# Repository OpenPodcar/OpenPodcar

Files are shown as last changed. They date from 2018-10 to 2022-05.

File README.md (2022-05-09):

# OpenPodcar

Open Source Hardware Design and Software for OpenPodcar.

https://user-images.githubusercontent.com/34858915/167230498-64ceeedd-7fe7-4e6d-a8b0-ddad5ff45466.mov

## Table of Contents
I. [General Info](#general-info)

II. [Bill of Materials](#bom)

III. [Software Setup](#software-setup)

IV. [Hardware Setup](#hardware-setup)

V. [User Guide](#user-guide)

VI. [General Testing](#general-testing)

VII. [3D Gazebo Simulation](#gazebo-simulation)

VIII. [Troubleshooting Guide](#troubleshooting-guide)

IX. [How to Contribute?](#how-to-contribute)

X. [Cite OpenPodcar](#cite-openpodcar)

XI. [Licence](#licence)

## I.  General Info

The OpenPodcar is an affordable and open source hardware and software platform for self-driving car research. It can be used for general autonomous vehicle research as well as for human-robot interaction (HRI) studies and practical automated transportation of people and goods.

The project includes:
- Hardware design and instruction to build and wire the physical car
- Arduino software for speed control
- Pololu software for steering control
- ROS drivers for the whole vehicle steering and speed
- Gazebo 3D simulation
- move_base and gmapping integration

To build the physical OpenPodcar, first obtain the components detailed in [Bill of Materials](#bom), then follow the steps of the build process detailed in [Software Setup](#software-setup), [Hardware Setup](#hardware-setup),  [General Testing](#general-testing) and [User Guide](#user-guide). The 3D simulation can be directly installed in [3D Gazebo Simulation](#simulation).

## II.  Bill of Materials
Obtain the following components, which are available from many commercial suppliers and some weblinks are suggested.

### 1. For the vehicle
- 1 Pihsiang TE-889XLSN hard-canopy scooter (branded in UK as ShopriderTraverso) e.g. [Link to product](https://romamedical.co.uk/shoprider-traveso/)
- 1 3D Velodyne Lidar (VLP-16) with its controller box e.g. [Link to product](https://velodynelidar.com/products/puck/)
- 1 laptop under linux Ubuntu 16.04 e.g. [Link to product](https://www.lenovo.com/gb/en/laptops/thinkpad/p-series/ThinkPad-P51/p/22TP2WPWP51)
- 1 Laptop or computer under Windows 7+
- 1 Gimson Robotics GLA750-P 12V DC linear actuator with position feedback (250mm stroke) e.g. [Link to product](https://gimsonrobotics.co.uk/categories/linear-actuators/products/gla750-p-12v-dc-linear-actuator-with-position-feedback)
- 1 ON/OF Toggle/Flick switch button e.g. [Link to product](https://www.ebay.co.uk/itm/12V-HEAVY-DUTY-25A-UNIVERSAL-METAL-SPRING-MOMENTARY-ON-OFF-TOGGLE-FLICK-SWITCH/231257116468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)
- 1 USB hub (with at least 3 USB ports) e.g. [Link to product](https://www.amazon.co.uk/AmazonBasics-4-Port-Ultra-Mini-Bus-powered/dp/B003M0NURK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)
- 1 USB A cable (Arduino <-> Laptop)
- 1 USB mini B cable (Pololu <-> Laptop)
- 1 Ethernet cable (Velodyne <-> Laptop) 
- 1 Deadman push button for the vehicle ignition system e.g. [Link to product](https://www.ebay.co.uk/itm/Philmore-30-825-SPST-Hand-Held-Push-Button-Switch-N-O/253746249505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)
- 1 3-meter rubber cable e.g. [Link to product](https://www.design-restoration-spares.com/product/real-rubber-cable-3-core-black/) 
- 1 Joystick with its USB cable e.g. [Link to product](https://www.logitechg.com/en-gb/products/space/extreme-3d-pro-joystick.942-000031.html)
- 1 Manfrotto Black Digi Table Tripod 709B e.g. [Link to product](https://www.manfrotto.com/ie-en/black-digi-table-tripod-709b/)
- 1 Inline car fuse e.g. [Link to product](https://www.ebay.co.uk/itm/BRAND-NEW-STANDARD-INLINE-CAR-FUSE-BLADE-HOLDER-30AMP-12V-SPLASH-PROOF-K265/170976134151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)
- 1 Fuse 7.5Amp
- 1 Relay e.g. [Link to product](https://www.ebay.co.uk/itm/164139969972?hash=item2637812db4:g:LqAAAOSwX9VefSO4)
- A few metric HEX bolts, nuts, flat washers and cap nuts
- A few cables ties

### 2. For the PCB
- 2 XL4016 Step-Down Buck converters DC-DC e.g. [Link to product](https://www.amazon.co.uk/dp/B086W6B9H1/ref=pe_27063361_485629781_TE_item?th=1)
- 1 Arduino Uno Rev3 e.g. [Link to product](http://store.arduino.cc/products/arduino-uno-rev3)
- 1 Pololu JRK 21v3 Motor Controller with Feedback e.g. [Link to product](https://coolcomponents.co.uk/products/jrk-21v3-usb-motor-controller-with-feedback-fully-assembled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)
- 1 MCP4725 DAC e.g. [Link to product](https://protosupplies.com/product/mcp4725-12-bit-dac-module/)
- 1 7-segment LCD with 3 digits e.g. [Link to product](https://www.alibaba.com/product-detail/Taidacent-Red-0-200V-Measurement-Range_60679181399.html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)
- 1 Velodyne controller box (comes with the Velodyne lidar)
- 1 10K Resistor
- 1 100K Resistor
- 2 Screw Terminal Block connectors e.g. [Link to product](https://www.amazon.co.uk/Universal-Connector-Calculators-Electronic-Equipments/dp/B0922KLC4K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)
- Male and female headers for Arduino and Pololu JRK 21v3 e.g. [Link to product](https://www.amazon.co.uk/dp/B07CWSXY7P/ref=pe_27063361_485629781_TE_item)
- A few M1.5, M2.5 and M3 bolts and nuts 

### 3. Tools
- Soldering station with solder
- Female and Male insulated electric connector crimp bullet terminals e.g. [Link to product](https://www.aliexpress.com/item/32874324815.html)
- Female and Male insulated crimp bullet terminals e.g. [Link to product](https://www.ebay.co.uk/itm/333917138391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)
- Power supply 24V or more e.g. [Link to product](https://www.amazon.co.uk/Lavolta-Variable-Linear-Bench-Supply/dp/B019KL4G6I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)
- Breadboard e.g. [Link to product](https://www.amazon.co.uk/K-H-RH-32-Solderless-Breadboard/dp/B07DNB74FV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)
- Multimeter e.g. [Link to product](https://www.machinemart.co.uk/p/clarke-cdm10c-digital-multimeter-5-function/)
- Gauge wires e.g. ~0.8mm, ~2mm and ~4mm diameter
- ELEGOO 120pcs Multicolored Dupont Wires 40pin Male to Female, 40pin Male to Male, 40pin Female to Female Breadboard Jumper Wires Ribbon Cables Kit Compatible with Arduino Projects [Link to product](https://www.amazon.com/Elegoo-EL-CP-004-Multicolored-Breadboard-arduino/dp/B01EV70C78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)
- Clamp meter e.g. [Link to product](https://www.tester.co.uk/uni-t-ut210b-clamp-meter)
- Flathead and Phillips screwdrivers, pliers and automatic wire stripper
- Spare fuses e.g. [Link to product](https://www.halfords.com/tools/fuses-electricals-and-fixings/fuses/)

## III.  Software Setup

### 1. Ubuntu 16.04 and ROS

The OpenPodcar software stack requires a laptop working under Ubuntu 16.04 and with ROS Kinetic and Gazebo 7 installed:
- [Ubuntu 16.04 installation](https://ubuntu.com/tutorials/install-ubuntu-desktop#1-overview)
- [ROS Kinetic + Gazebo 7 installtion](http://wiki.ros.org/kinetic/Installation/Ubuntu)
- Clone this project repository somewhere on the laptop

**NB:** `Pololu JRK Configuration Utility` tool is a Windows app, which does not work on linux.

### 2. Arduino
- Install Arduino IDE on the Ubuntu laptop, instructions can be found [here](https://ubuntu.com/tutorials/install-the-arduino-ide#1-overview)
- Download the MCP4725 library file and place it into Arduino's `LIBRARIES` folder
- Arduino firmware source is supplied in `physicalVehicleNonRos/Arduino/ThrottleControlSerial.ino`
- Connect the Arduino USB cable to the laptop
- Open the `ThrottleControlSerial.ino` file in Arduino IDE
- Click on "**Upload**"
- **Acceptance Testing**
	- click on "**Tools**", then "**Serial Monitor**" 
	- set baudrate to 115000
	- type in some commands such as:
		- "**FA:170**" for zeroing
		- "**FA:210**" for forward speed
		- "**FA:120**" for reverse speed
	- the serial monitor should display the command that was typed in and the corresponding DAC value
	
### 3. Pololu JRK 21v3 Configuration

- Download Pololu's Windows Configuration Tool `Pololu JRK Configuration Utility` on a Windows  computer by following these steps [here](https://www.pololu.com/docs/0J38/3.a).
- To configure the Pololu, please follow the instructions [here](https://www.pololu.com/docs/0J38/5).
- For OpenPodCar, the steps below are followed:
	- Connect the Pololu USB cable to the Windows computer and open `Pololu Jrk Configuration Utility` tool

	- Go to "**Input**" tab: 
		- set "**Input mode**" to "**serial**"
		- keep all other parameters to default values
		- Final settings should like in the figure below:
		
	<p align="center">
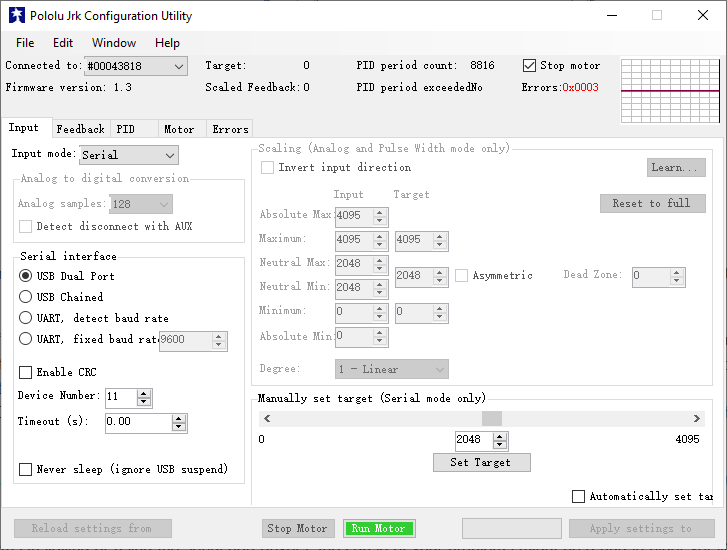
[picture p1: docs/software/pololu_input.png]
Pololu Input tab
	
	</p>

	- Go to "**Feedback**" tab:
		- set "**Feedback mode**" to "**Analog voltage**"
		- check "**Invert feedback direction**"
		- Under "**Calibration**":
			- set "**Absolute Max**" to "**2600**"
			- set "**Maximum**" to "**2600**"
			- set "**Minimum**" to "**1000**"
			- set "**Absolute Min**" to "**1000**"
			- keep all other paramters to default values
		- Final settings should like in the figure below:
	
	<p align="center">
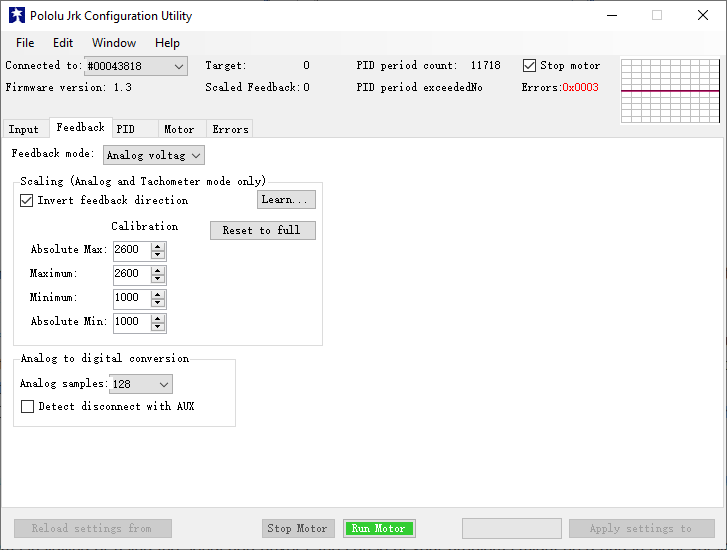
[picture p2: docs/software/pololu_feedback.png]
Pololu Feedback tab
	
	</p>

	- Go to "**PID**" tab:
		- set "**Proportional Coefficient**" to "**6**" at the top and "**1**" at the bottom, so that to get a final "**3**"
		- keep all other parameters to default values 
		- Final settings should like in the figure below:

	<p align="center">
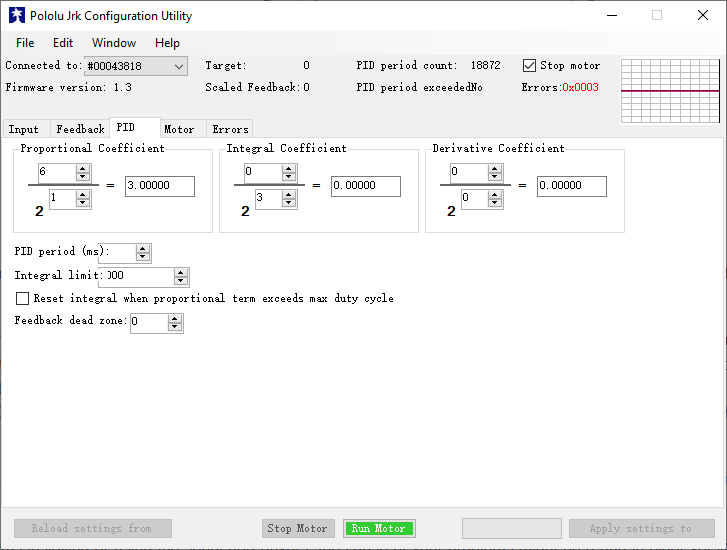
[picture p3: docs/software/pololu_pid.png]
Pololu PID tab
	
	</p>

	- Go to "**Motor**" tab:
		- check "**Invert motor direct**"
		- in the "**Forward column**", set "**Max. current (A)**" to "**0**"
		- keep all other parameters to default values
		- Final settings should like in the figure below:
		
	<p align="center">
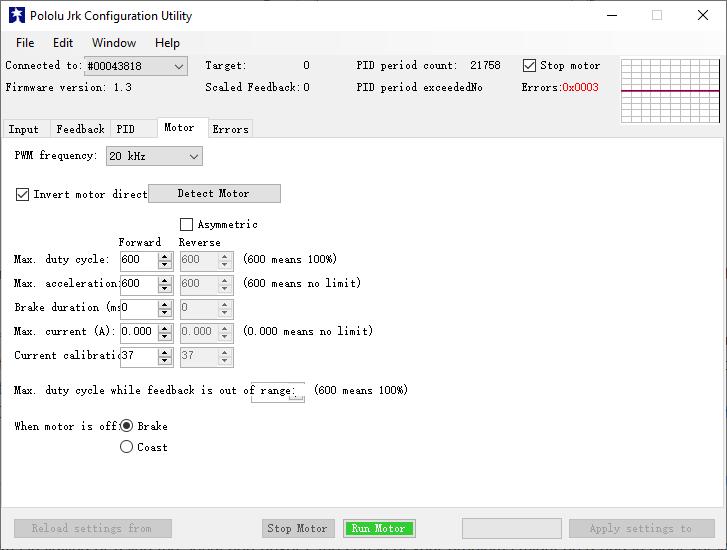
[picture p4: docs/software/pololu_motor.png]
Pololu Motor tab
	
	</p>

	- Go to "**Error**" tab:
		- you should see a window similar to the figure below with some red flags on	
		- set "**No power**", "**Motor driver error**", "**Feedback disconnected**" and "**Max. current exceeded**" to "**Enabled and latched**"
		- click on "**Clear**" and "**Reset**"
		
	<p align="center">
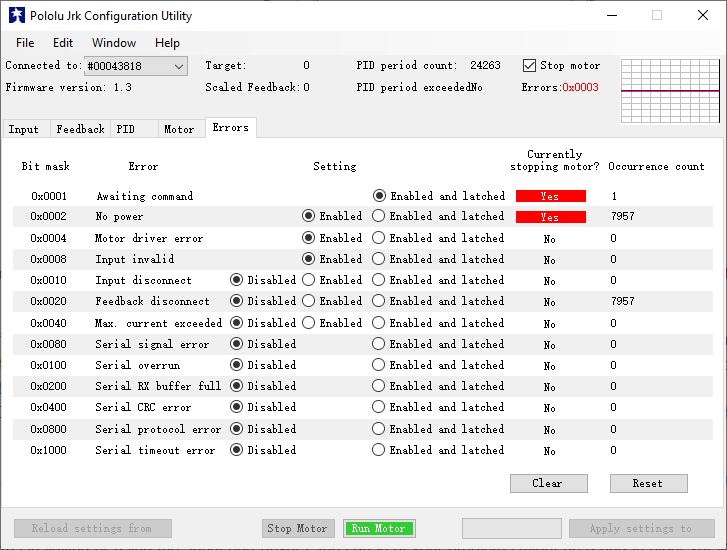
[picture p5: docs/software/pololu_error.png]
Pololu Error tab
	
	</p>

	- Click on "**Apply settings to**"

### 4. Simlink for USB COM Ports

Here, the goal is to create persistent USB serial device names (aka Simlink) for the Arduino and the Pololu.

- In a terminal, type: `sudo nano /etc/udev/rules.d/99-tty.rules`
- Connect the Arduino and the pololu USB cables to the linux laptop using a USB hub, then type in the terminal:
```
sudo lsusb -v | grep 'idVendor\|idProduct\|iSerial'
```
- The above command displays the idVendor and idProduct for all the serial devices connected to your laptop and needs to be reported in the Simlink. 
- Copy the following lines in `99-tty.rules` file:
```
#Arduino com-port rules
SUBSYSTEM=="tty", ATTRS{idVendor}=="2341", ATTRS{idProduct}=="0043", SYMLINK+="ttyArduino", GROUP="dialout", MODE="0666"
#Pololu com-port rules -- NB the pololu has two virtual serial ports on a single USB interface.
SUBSYSTEM=="tty", ATTRS{idVendor} =="1ffb", ENV{ID_USB_INTERFACE_NUM}=="00"  SYMLINK+="ttyPololuCOM"
SUBSYSTEM=="tty", ATTRS{idVendor} =="1ffb", ENV{ID_USB_INTERFACE_NUM}=="02"  SYMLINK+="ttyPololuTTL"
```
- Save and close `99-tty.rules` file
- Then type in the terminal `sudo reboot`
- Check the status of each SimLink by typing in terminal for example: `ls -l /dev/ttyArduino` or `ls -l /dev/ttyPololuCOM`

### 5. Velodyne 3D Lidar Configuration for ROS

The lidar needs to be set up over Ethernet. The laptop must be on a wired network, not wifi. The IPs must be configured as in the velodyne, the default lidar IP is 192.168.1.201.

Follow the Velodyne installation instructions for ROS from [here](http://wiki.ros.org/velodyne/Tutorials/Getting%20Started%20with%20the%20Velodyne%20VLP16).

## IV.  Hardware Setup

### A. Doors and Seat Removal

- Remove the screws from the hinges in order to remove the doors.
- Remove the seat by following the instructions given in the vehicle service manual.

### B. Linear Actuator

Before mounting the linear actuator under the vehicle, first acceptance test it with the Pololu to check that it is functional.

#### 1. Acceptance Testing

This section shows how to test the linear actuactor before mounting it.

- Material: Gimson linear actuator, Pololu JRK 21v3 Configuration Tool, power supply, a breadboard, some wires (~0.8mm diameter) e.g. Dupont wires, a multimeter
- Wire the power supply "**-**" to Pololu's "**GND**"
- Wire the power supply "**+**"  to Pololu's "**VIN**" 
- Wire the linear actuator's "**black wire**" to Pololu's "**A**"
- Wire the linear actuator's "**red wire**" to Pololu's "**B**"
- Use the breadboard to make the following connections:
	- Wire the linear actuator's "**blue wire**" to Pololu's "**FB**" 
	- Wire the linear actuator's "**yellow wire**" to Pololu's "**+5V**" (i.e. pin below "**FB**")
	- Wire the linear actuator's "**white wire**" to Pololu's "**GND**" (i.e. pin below "**+5V**")
	- Set the external power to supply 12V -> the Pololu LED should start blinking orange
	- Connect the Pololu USB to a computer with the "**Pololu Jrk Configuration Utility**" Tool
- Open the Configuration Tool Interface and go to the "**Error**" tab to check that no error is displayed other than the flag "**Awaiting command**". 
	- If there are errors, click on "**Reset**" and "**Clear**" until the Poolu's LED start blinking green
	- Go to "**Input**" tab and use the cursor or type to send commands to the linear actuator, then click on "**Set Target**" e.g.
	- "2500" : the linear actuator should extend its length to a maximum
	- "1500" : the linear actuor should reduce its length
	- "1900" : the linear actuator should have a medium length. **Note**: this is the position that the linear actuator should have when mounting it underneath the vehicle.
		
#### 2. Access the underside of the vehicle

To access the underside of the vehicle, this requires the help of at least three people.

- Material: 2 axle stands, 2 jacks
- Bring in two axle stands and set them as high as about 75cm each
- Place the two axle stands about one meter away from the front and back wheels, both on the same side of the vehicle, as shown in red in the picture below.
	
	<p align="center">
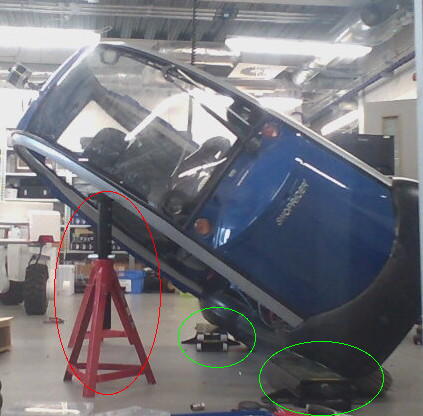
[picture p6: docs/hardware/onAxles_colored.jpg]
Vehicle tilted using on axles and jacks
	
	</p>
	
- Place two jacks right next to the front and back wheels, on the same side as the axle stands as shown in green in the above picture
- One person should stand next to each axle stand
- Another person should stand on the other side of the vehicle and push the vehicle from the top towards the people next to the axle stands
- The persons next to the axle stands should adjust the positions of the stands in order to get the vehicle nicely tilted without any instability
- The vehicle should now be tilted on one side and its underside clearly visible in order to mount the linear actuactor
 
#### 3. Mounting

```diff
- MOUNTING THE LINEAR REQUIRES DRILLING THROUGH STEEL USING A SUITABLE POWERFUL DRILL AND QUALIFIED OPERATOR. 
- THERE IS POTENTIAL FOR INJURY TO UNQUALIFIED OPERATORS. THIS IS THE ONLY BUILD STEP WHICH REQUIRES A QUALIFIED OPERATOR.
```

- Material: Gimson linear actuator, a drill capable of drilling steel, 2 M6 HEX head bolts, 2 HEX nuts, 2 cap hex nuts and a few flat washers with 8mm diameter
- The linear actuator must have a medium length obtained via the Pololu command "1900", cf. the **Acceptance Testing** detailed above. 
- There is an existing hole in the triangular part of chassis next to the right front wheel axle, shown in the figure below in the green circle. Fix the front hole of the linear actuator to this  using an M6 bolt, nut, several washers and a cap nut
- Drill a new M6 hole on the left side of the front chassis at the location shown by the red circle in the photo below.
- Fix the back of the linear actuactor to the newly drilled hole using an M6 bolt and nuts, via washers
- The final mounting is shown in the photo below.
	
	<p align="center">
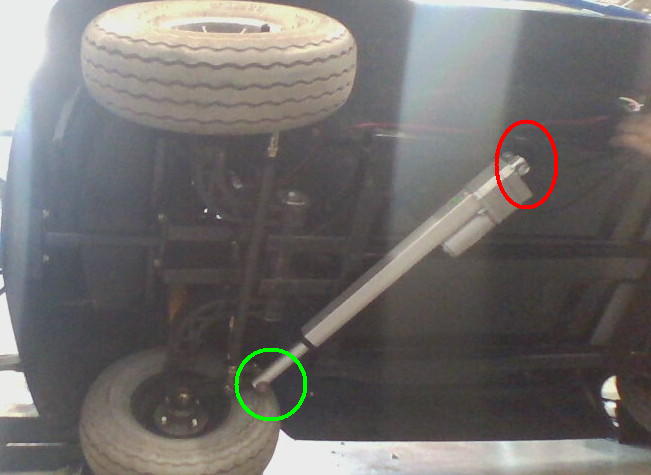
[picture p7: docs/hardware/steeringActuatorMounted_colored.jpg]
Linear actuator mounted underneath the vehicle
	
	</p>

- Once the mounting is finished, bring the podcar back to its normal position (requires again at least 3 people). 
- Remove the axle stands and jacks before making the integration test of the linear actuactor.

#### 4. Integration Test

This final test will helps to verify that the linear actuactor is well mounted and can steer the wheels as expected:

- Repeat the **Acceptance Testing** protocol presented above, but this time with the linear actuactor mounted under the vehicle, its wires can pass through an empty area between the vehicle plastic bumper and the left battery, and send some commands such as:
- a "2500" command should steer the front wheel to the far right, i.e about -45 deg
- a "1900" command should keep the front wheels facing forward, i.e. about 0 deg
- a "1000" command should steer the front wheels to the far left, i.e. about +45 deg
		
### C. ON/OFF Switch and Fusing

- Material: inline car fuse, fuse 7.5Amp, ON/OFF switch, x2 12V batteries (the ones already part of the vehicle, under the seatback), some wires (use ~4mm diameter for fuse, switch and batteries, ~2mm diameter for the buck converters)
- Switch off the vehicle batteries completely, switch is under the vehicle seatback
- Fix a wire using a crimp bullet terminal onto each pin of the switch
- Get access to the right battery's "**+**" pole and use a plier to unscrew the bolt and flat washer as shown below.

	<p align="center">
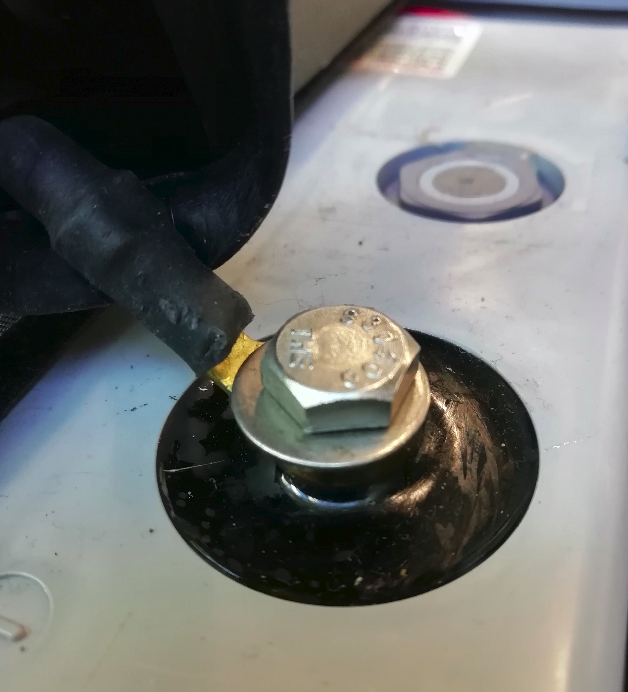
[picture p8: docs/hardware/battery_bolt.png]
Battery bolt and washer already screwed
	
	</p>

- Strip the wire on the "**+**" pin of the switch by 3cm and connect it to the "**+**" of the right battery by tangling it around the battery "**+**" pole
- Screw back the bolt and flat washer that were removed from the battery "**+**" pole
- Insert the 7.5Amp fuse inside the inline car fuse
- Connect the inline car fuse "**-**" wire to the switch "**-**" pin
- Extend the inline fuse "**+**" wire by 30cm such as soldering another wire to it, then keep it safely for later connection with the buck converter "**+**" on the PCB board
- Get access to the left battery's "**-**" pole's wire, strip a small area in the middle and plug a new and long wire (~50cm) there, then keep this new wire safely for later connection with the buck converter "**-**" on the PCB board as shown below.

	<p align="center">
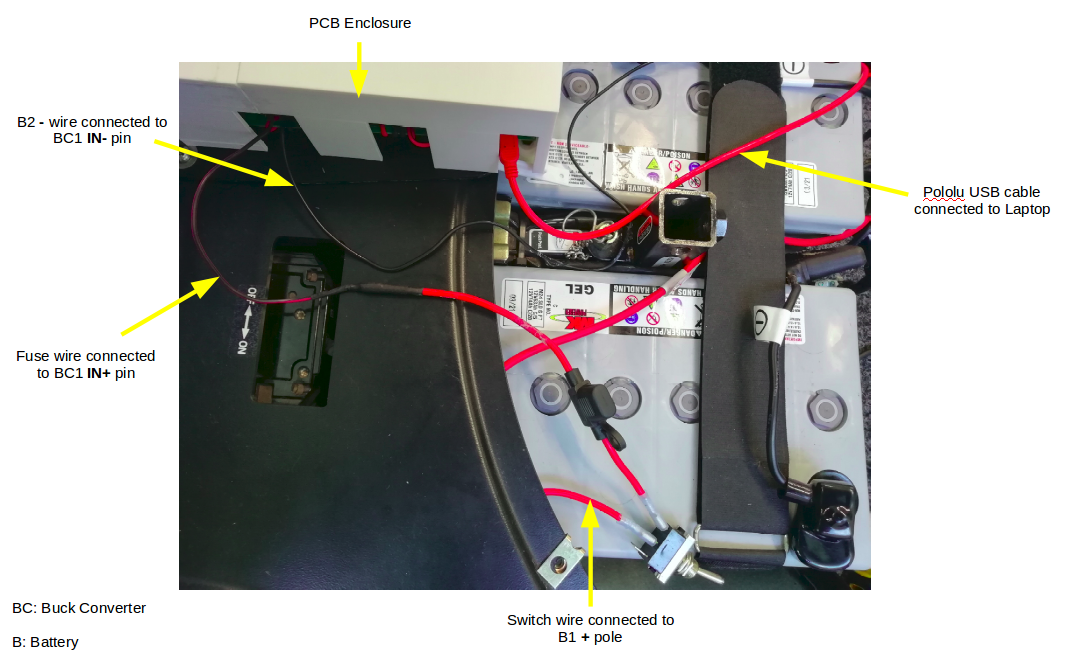
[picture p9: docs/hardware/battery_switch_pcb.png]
Battery, switch and PCB connections
	
	</p>

### D. 3D Lidar

- Material: 3D lidar, tripod, a drill, 3 cable ties 
- Place the tripod on the vehicle's roof as shown in the photo below and use a marker to mark the positions of its three feet.	

	<p align="center">
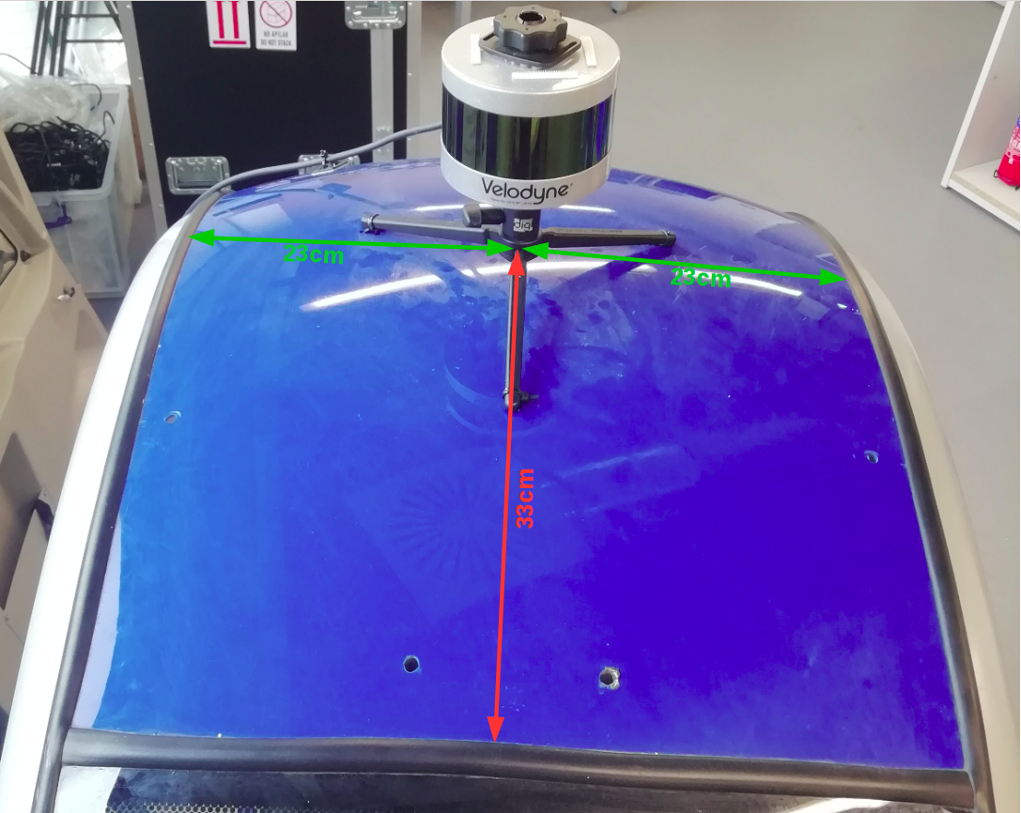
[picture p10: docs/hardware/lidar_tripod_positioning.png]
Lidar tripod positioning
	
	</p>

- Remove the tripod from the roof
- Drill two holes, ~0.6mm diameter each and their centers separated by about 1cm, on either side of each marked position as shown in the photo below.

	<p align="center">
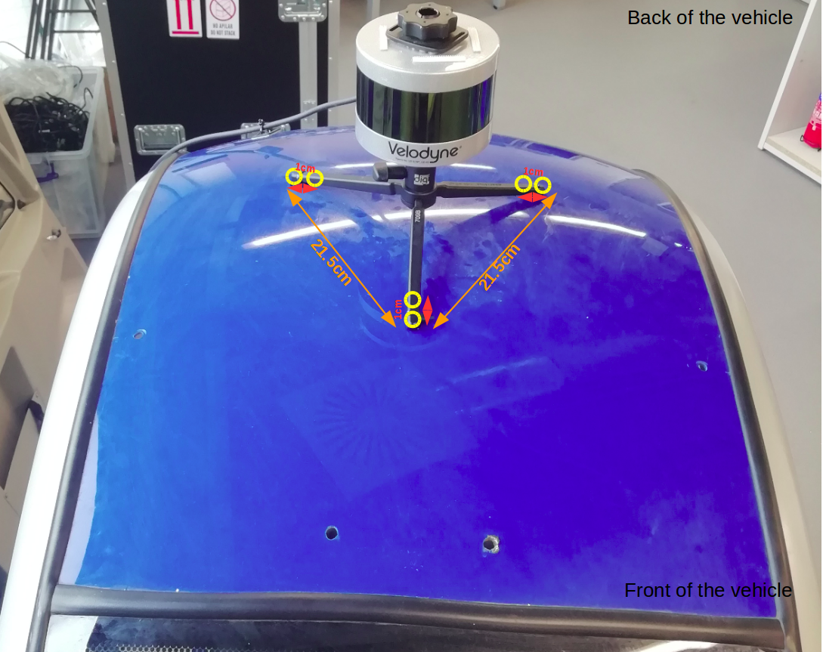
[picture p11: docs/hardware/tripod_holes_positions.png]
Tripod holes positions
	
	</p>

- Screw the lidar onto the tripod
- Place the tripod back on the roof
- Use the cable ties, each passed through one pair of drilled holes and around a tripod foot, to secure the tripod to the roof as shown in the photo below. (may require the intervention of two people)

	<p align="center">
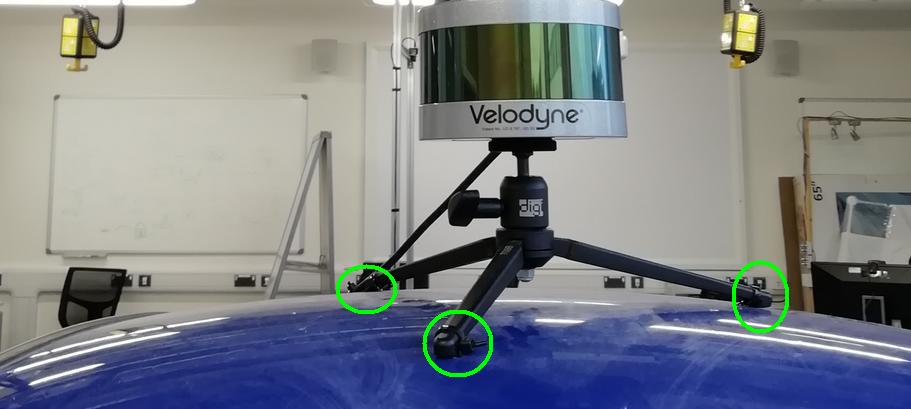
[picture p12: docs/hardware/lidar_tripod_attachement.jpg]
Tripod attachment to the vehicle
	
	</p>

### E. Buck Converters

Here, the buck converters' voltage and current will set to the desired values and then tested.

- Material: buck converters, power supply, multimeter, electronics flathead screwdriver, clamp meter and some wires (~2mm diameter)

#### 1. XL4016 Buck converter 1

1. Wire the power supply "**+**" to the buck converter's "**IN+**" terminal block using a screwdriver
2. Wire the power supply "**-**" to the buck converter's "**IN-**" terminal block using a screwdriver
3. Insert a wire into the buck converter's "**OUT+**" terminal block and keep the other side of the wire safely aside
4. Insert a wire into the buck converter's "**OUT-**" terminal block and keep the other side of the wire safely aside
5. Set the power supply to 24V and turn it on
6. Use the multimeter to measure the "**voltage**" between the buck converter's "**OUT+**" and "**OUT-**"
7. Whilst reading the multimeter, use a screw driver to turn the **potentiometer P1** on the buck converter until the desired output voltage of 16V is reached (or the voltage required for the linux laptop)
8. **Voltage Testing:** 
	- Turn off the power supply and stop using th screw driver
	- Turn on the power supply back to 24V
	- Use the multimeter to check that the **voltage** between the buck converter's "**OUT+**" and "**OUT-**" is indeed 16V
	- If not, then repeat steps 5 to 8
9. Use the multimeter to measure the **current** between the buck converter's "**OUT+**" and "**OUT-**"
10. Whilst reading the multimeter, use a screw driver to turn the **potentiometer P2** on the buck converter until the desired output current of 3.75A is reached (or the maximum current required for the linux laptop)
11. **Current Testing**
	- Turn off the power supply and stop using th screw driver
	- Turn on the power supply back to 24V
	- Use the clamp meter to check that the **current** going out of the buck converter's "**OUT+**" wire is indeed 3.75A
	- If not, then repeat steps 9 to 11
		
#### 2. XL4016 Buck converter 2

1. Wire the power supply "**+**" to the buck converter's "**IN+**" terminal block using a screwdriver
2. Wire the power supply "**-**" to the buck converter's "**IN-**" terminal block using a screwdriver
3. Insert a wire into the buck converter's "**OUT+**" terminal block and keep the other side of the wire safely aside
4. Insert a wire into the buck converter's "**OUT-**" terminal block and keep the other side of the wire safely aside
5. Set the power supply to 24V and turn it on
6. Use the multimeter to measure the **voltage** between the buck converter's "**OUT+**" and "**OUT-**"
7. Whilst reading the multimeter, use a screw driver to turn the **potentiometer P1** on the buck converter until the desired output voltage of 12V is reached (or the voltage required for the Pololu and 3D Lidar)
8. **Voltage Testing** 
	- Turn off the power supply and stop using th screw driver
	- Turn on the power supply back to 24V
	- Use the multimeter to check that the **voltage** between the buck converter's "**OUT+**" and "**OUT-**" is indeed 12V
	- If not, then repeat steps 5 to 8
9. Use the multimeter to measure the **current** between the buck converter's "**OUT+**" and "**OUT-**"
10. Whilst reading the multimeter, use a screw driver to turn the **potentiometer P2** on the buck converter and set the desired output current of 3A is reached (or the maximum current required for the linear actuator and 3D Lidar)
11. **Current Testing**
	- Turn off the power supply and stop using th screw driver
	- Turn on the power supply back to 24V
	- Use the clamp meter to check that the **current** going out of the buck converter's "**OUT+**" is indeed 3A
	- If not, then repeat steps 9 to 11
			
### F. MCP4725 DAC

- Solder the male headers onto the DAC board pins.
- **Acceptance Testing**
	- Material: MCP4725 DAC, Arduino, some wires (~0.8mm diameter) e.g. female to male Dupont wires, a breadboard, a multimeter
	- Use a breadboard to make the following connections:
		- Wire both DAC "**GND**" to both Arduino "**GND**", using two female to male wires
		- Wire the DAC "**VCC**" to Arduino "**5V**", using a female to female wire
		- Wire the DAC "**SDA**" to Arduino "**SDA**", using a female to male wire
		- Wire the DAC "**SCL**" to Arduino "**SCL**", using a female to male wire
		- Wire the DAC "**OUT**" to an isolated point on the breadboard, using a female to female wire
	- Connect the Arduino USB cable to a computer port
	- Use the multimeter to measure the voltage received on the DAC:
		- Voltage between the DAC "**GND**" and "**VCC**" should give a value between "**4.7V**" to "**5V**" i.e. equivalent to Arduino input voltage
		- Voltage between the DAC "**GND**" and "**OUT**" should give a value between **1.9V** and **2.4V**
			
### G. 3D Printing
The following items need to be 3D printed, the files are located under `physicalVehicleNonRos/3D_parts`:
- The LCD display support part is `LCD_support.stl`
- The Velodyne Lidar support part is `VLP16_support.stl` 
- The PCB enclosure is divided into several stl files available in `PCB_enclosure/`

### H. Printed Circuit Board (PCB)

Manufacture the PCB board by sending the gerber zip files `physicalVehicleNonRos/PCB/gerber.zip` to an online PCB manufacturer such as (https://www.pcbway.com). They will then post the bare board to you, usually in a few days. At this stage there are no components on it, you will solder them on later in these instructions. **NB**: You may wish to order several copies of the PCB in case of manufacturing errors or if you break one or more of them.
	
#### 1. Acceptance Testing

- Material: manufactured PCB board, multimeter
- Use the multimeter in continuity mode (diode symbol) to check each one of the PCB connections. If a connection on the board is continuous i.e. good, then the multimeter emits a continuous **beep**  (takes around 5 minutes in total). If any connection is not good then the manufactured PCB board is faulty and should not be used.

#### 2. Assembly

- Material: manufactured PCB board, soldering station with solder, headers, Arduino, Pololu, resistors (100K and 10K), 3D printed parts for LCD display and lidar, bolts and nuts
- Solder a 10K resistor on R2 location
- Solder a 100K resistor on R1 location
- Solder male headers on the Arduino location
- Solder the two terminal blocks to their respective locations 
- Solder female headers for the Pololu and the DAC
- Solder the buck converter input and output wires to the respective pins on the board
- Mount the Arduino, Pololu and DAC onto their headers on the PCB board
- Use M3 bolts and nuts to fix the lidar controller box onto the lidar 3D printed support
- Use M3 bolts and nuts to fix the buck converters, Arduino, LCD display and lidar support with controller box onto the PCB board
- USe M1.5 bolts and nuts to fix the DAC onto the board
- Use M2.5 bolts and nuts to fix the Pololu onto the board

#### 3. Integration Testing

- Material: power supply, multimeter, some wires (~2mm diameter)
- Connect wires between the power supply and buck converter 1's "**IN+**" and "**IN-**"
- Measure the voltage across the PCB components, check the safety of the board and ensure that the components (especially Arduino, buck converters and DAC) work as expected, as shown in the figure below.

	<p align="center">
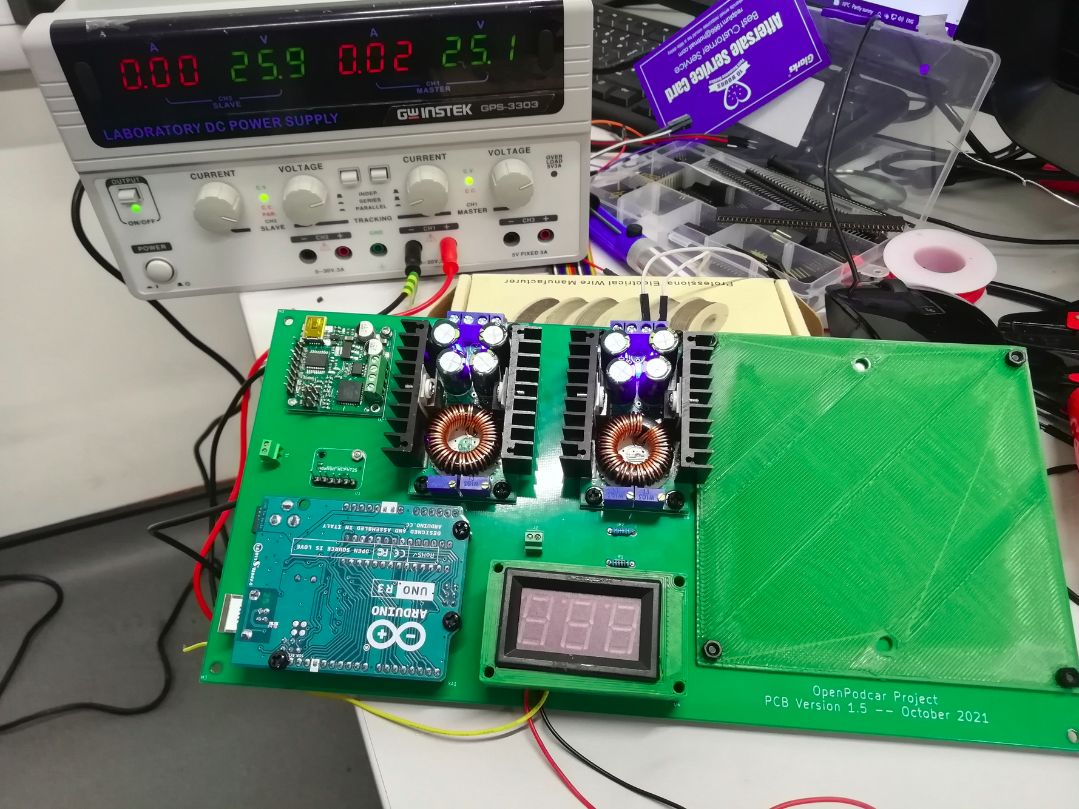
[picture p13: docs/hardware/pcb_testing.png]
PCB board integration testing
	
	</p>

### I. Vehicle Connections

#### A. DeadMan Handle (DMH) and Relay

This step explains how to integrate a DMH and a relay in order to control the vehicle ignition system. The addition of the Relay and the DMH Switch are essential for safe operation, especially where new unproven autonomous control systems are in development. A two stage approach is used to reduce this risk. Refer to the schematic diagram DMH section in conjunction with this description.

- Material: 1 deadman push button, 1 relay, some wires (~2mm diameter), 3-meter rubber cable, female and male insulated electric connector crimp bullet terminals, plier, flathead screwdriver
- For the relay: 
	- Connect a 2-meter wire to the relay's "**-**" pin 
	- Connect a 2-meter wire to  both the relay pins "**S**" and "**+**"
	- The relay wires should be as shown in the photo below

		<p align="center">
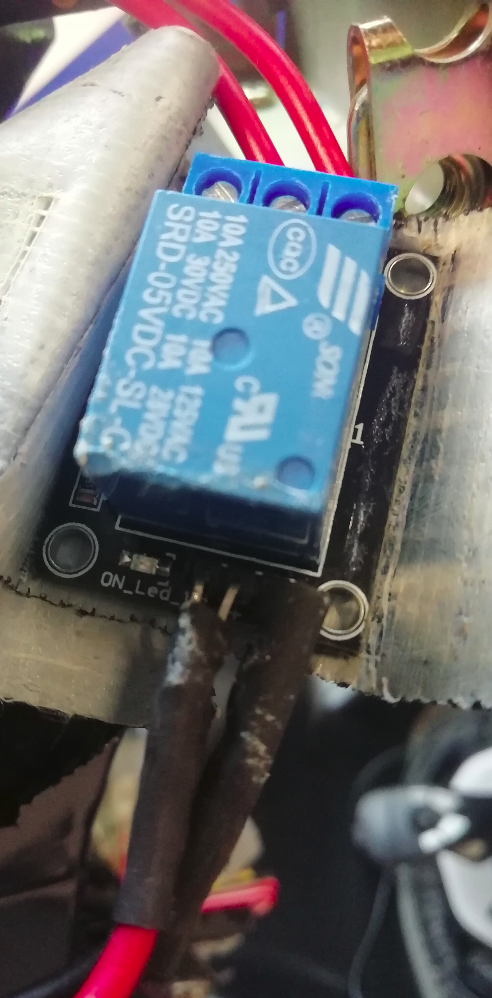
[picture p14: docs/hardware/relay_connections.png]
Relay's connections
		
		</p>
		
	- Use electrical insulating tape to wrap the relay with as shown below.
	
		<p align="center">
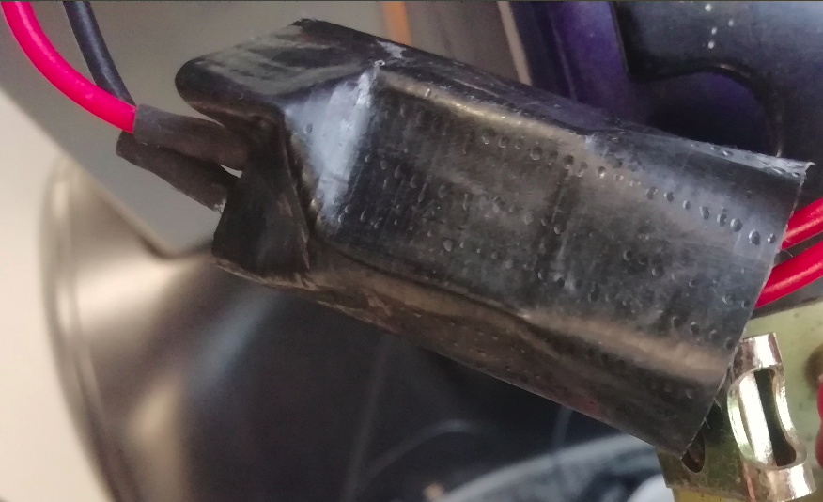
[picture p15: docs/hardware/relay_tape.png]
Relay wrapped with electrical insulating tape
		
		</p>
	
	- Use a plier to cut the two wires **brown** and **blue** connected to the vehicle ignition key	
	- Attach a female insulated electric connector crimp bullet terminal to the **blue** wire directly connected to the ignition key for safety reasons
	- Attach a female insulated electric connector crimp bullet terminal to the **brown** wire directly connected to the ignition key for safety reasons
	- Connect the relay's "**COM**" pin to the ignition **brown** wire coming from the vehicle steering column using a female insulated electric connector crimp bullet terminal
	- Connect the relay's "**NO**" pin to the ignition **blue** wire coming from the vehicle steering column using a female insulated electric connector crimp bullet terminal

- For the DMH: 
	- Connect the 3-meter rubber cable to the deadman push button
	- Connect the DMH cable to the wire linking the relay "**NO**" pin and the ignition **blue** wire as shown in the photo and the circuit diagram below:
	
	<p align="center">
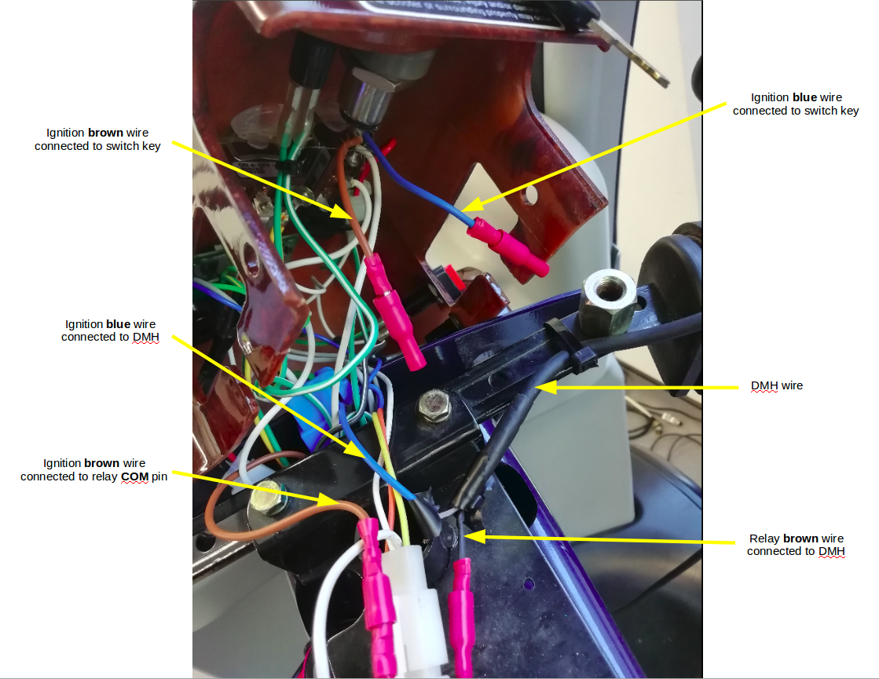
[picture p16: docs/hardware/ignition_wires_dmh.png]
Vehicle ignition wires connected to DMH and relay
	
	</p>	

	<p align="center">
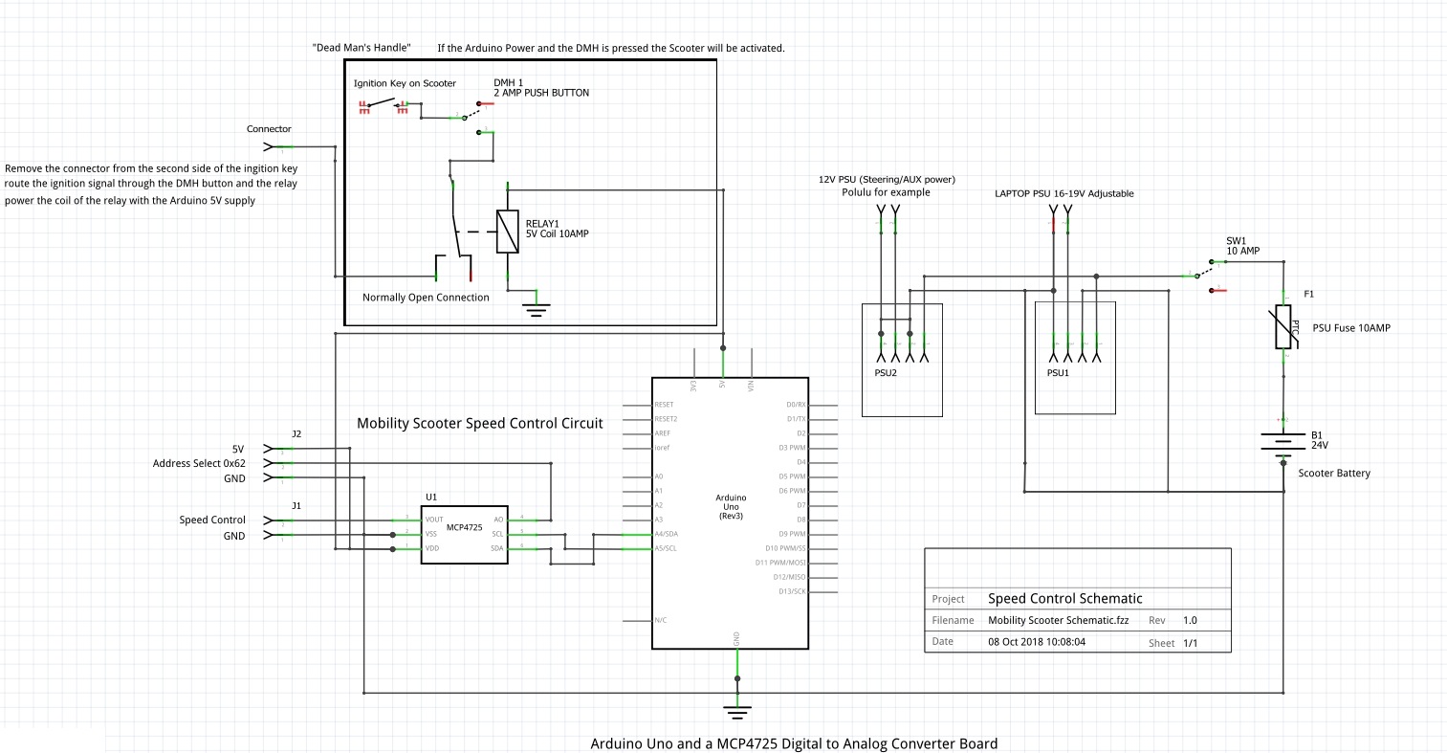
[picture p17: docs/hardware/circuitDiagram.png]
Vehicle circuit diagram
	
	</p>	

#### B. Speed Potentiometer 

- Material: some wires (~2mm diameter), soldering station with solder, 1 plastic screw terminal block 2x2
- De-solder the middle pin of the vehicle potentiometer (white wire) and connect it to a 2-meter long wire inserted into the plastic terminal block "**+**" pin
- Solder a 2-meter long wire next to the potentiometer pin on the left with a yellow wire and insert in its other length into the plastic terminal block "**-**" pin

#### C. PCB connections

- Material: soldering iron, flathead screwdriver
- Solder the other side of the relay's "**+**" and "**S**" pins wire to the LCD display "**VIN**" pin on the PCB board
- Solder the other side of the relay's "**GND**" to the LCD display "**GND**" pin on the PCB board
- Insert the lidar controller box "**+**" wire to the PCB terminal block "**+**" pin (NB: another option would be to solder the wire) 
- Insert the lidar controller box "**-**" wire to the PCB terminal block "**-**" pin (NB: another option would be to solder the wire) 
- Connect the DAC "**VOUT**" to the plastic terminal block "**+**" pin linked to the vehicle speed potentiometer 
- Connect the DAC "**GND**" to the plastic terminal block "**-**" pin linked to the vehicle speed potentiometer
- Connect the LCD display "**SIG**" wire to the plastic terminal block "**+**" pin linked to the vehicle speed potentiometer 
- Connect the inline car fuse "**+**" wire (earlier set aside) to buck converter 1's "**IN+**" pin
- Connect the inline car fuse "**-**" wire (earlier set aside) to buck converter 1's "**IN-**" pin

#### D. Connect the linear actuactor to the Pololu JRK 21v3

- Material: flathead screwdriver, Pololu, linear actuactor, some wires (~0.8mm)
- Wire the linear actuator's **black wire** to Pololu's "**A**"
- Wire the linear actuator's **red wire** to Pololu's "**B**"
- Wire the linear actuator's **blue wire** to Pololu's "**FB**" 
- Wire the linear actuator's **yellow wire** to Pololu's "**+5V**" (i.e. pin below "**FB**")
- Wire the linear actuator's **white wire** to Pololu's "**GND**" (i.e. pin below "**+5V**")

## V.  General Testing

This section generally explains some steps to test the general functioning of the vehicle speed, steering, detection and tracking systems.

### A. Speed control

Implementing and testing this speed system should be undertaken with the drive wheels of the vehicle raised off of the ground, allowing for checks to be made of the DMH without the risk of the vehicle speeding off out of control.

- Material: jacks
- Place the jacks on both of the vehicle to raise its wheels off of the ground
- open a terminal and type `cd physicalVehicleNonRos/testingTools/`
- while pressing on the DMH:
	- type `python zeroSpeed.py` to zero the speed
	- type `python fastSpeed.py` to move the vehicle forward (speed commands can be modified)
	- type `python slowSpeed.py` to move the vehicle backward (speed commands can be modified)

The Arduino serial monitor could be used to send speed commands.

### B. Steering Control

The steering and Pololu can be tested with a C++ executable `JrkCmd`. 
- Connect the Pololu USB to the vehicle laptop 
- Open a terminal and make sure `physicalVehicleNonRos/testingTools/JrkCmd` has the permission to be an executable
- type `./OpenPodcar/podcar/physicalVehicleNonRos/testingTools/JrkCmd Val` where "Val" is the desired command e.g. "1900" (straight), "2100" (turning slightly on the right), "1700" (turning slightly on the left) etc. 

**NB**:"Val" should be a value between "1000" (fully turned left) and "2500" (fully turned right).

### C. Object Detection and Tracking

To test the object detector and tracker:
- record a ROS bag file with some pedestrians appearing in it
- change the path of the bag file in `flobot_tracker.launch` to that of the newly recorded bag file
- open a terminal and type:
```
cd OpenPodcar/catkin_ws/src/FLOBOT
source devel/setup.bash
roslaunch flobot_tracker_bringup flobot_tracker.launch
```
An example video with detection and tracking results is shown below.

https://user-images.githubusercontent.com/34858915/167274773-8bbdb3f9-5252-4947-8f6d-412974ba1c71.mov

## VI.  User Guide 

### A. General Verification 

Perform the following actions and verifications before attempting to drive the vehicle:

- Check that the vehicle’s original lever for auto-manual is set to auto (DOWN). It is on the main motor, under the vehicle at the rear left, colored red. Requires some force to move it.

- Power on the vehicle using the original on-off switch located under the seat on the left. It is marked ON-OFF.

- Power on the modified electronics using the new toggle switch.   (This lights LEDs on the DCDCs and Pololu, and the lidar makes a whirring sound).

- Check that the batteries are charged (use a multimeter across one of the DCDC converters, need to see 24V or over. {\em Do not use the vehicle if it is undercharged, this is dangerous.}

- Power on the laptop

- Connect the lidar Ethernet cable to the laptop

- Connect the Joystick, Pololu and Arduino USB cables to the USB hub

- Connect the USB hub cable to the laptop USB port

- Check that the Pololu LED flashes green

- Check that the Arduino LED is green

- Check that the LCD display shows a voltage between 1.9V and 2.1V

- Press on the DMH push button and check that there is no beep

### B. Remote Control
 
The vehicle can be remotely-controlled using a joystick as follows:
- Modify this line ` <include file="/YourPath/OpenPodcar/podcar/catkin_ws/src/velodyne/velodyne_pointcloud/launch/VLP16_points.launch"/>` in `launch/podcar.launch` to correspond to the global path of Velodyne point_cloud launch file in the laptop
- Open a terminal and type:
```
cd OpenPodcar/catkin_ws/src/podcar
source devel/setup.bash
roslaunch podcar podcar.launch
```

If there is no error, the vehicle can then be simply controlled with the joystick as follows:
- move the Y-axis for speed control
- move X-axis for steering control

The video below shows a remote control drive of the OpenPodcar by a passenger.

https://user-images.githubusercontent.com/34858915/167232380-c03a253a-c92c-4cf6-9b76-fccac6fb3c3a.mov

### C. Move_base Control

This section explains how to drive the OpenPodcar in autonomous control mode using GMapping, move_base and the TEB planner.
- Change this line ` <include file="/YourPath/OpenPodcar/podcar/catkin_ws/src/velodyne/velodyne_pointcloud/launch/VLP16_points.launch"/>` in `launch/podcarsim2real_laser_scan_matcher.launch`to correspond to the global path of Velodyne point_cloud launch file in the laptop
- open a first terminal and type:
```
cd OpenPodcar/catkin_ws/src/podcar
source devel/setup.bash
roslaunch podcar podcarsim2real_laser_scan_matcher.launch
```
- open a second terminal and type:
```
cd OpenPodcar/catkin_ws/src/podcar
source devel/setup.bash
roslaunch podcar podcarsim_moveBase_sim2real.launch
```

At this stage, two options are available to send goal commands to the vehicle:
- Option 1: RViz GUI
	- Use RViz graphical user interface to set **2D Nav goal** commands to the vehicle using the green arrow. 
	
	An example of such control is shown in the following video for the vehicle parallel parking demo.

https://user-images.githubusercontent.com/34858915/167232813-bf33fbd5-f6af-4437-8bf9-8230338dea82.mov

- Option 2: Terminal 

	- open a third terminal and type:
	```
	cd OpenPodcar/catkin_ws/src/podcar
	source devel/setup.bash
	rostopic pub /move_base_simple/goal geometry_msgs/PoseStamped "frame_id: 'map' pose: position: x: 2.0 y: 0.0 z: 0.0 orientation: x: 0.0 y: 0.0 z: 0.0 w: 1.0"
	```
	
	This example command will move the vehicle 2m forward in **map** frame whilst keeping the same default orientation.
		
	Note: the vehicle orientation is formed by the quaternion: x, y, z and w. Euler angles can be converted to quaternions, for example using this [visualisation tool](https://quaternions.online/)
	
An example of the terminal based goal command is shown in the video below.

https://user-images.githubusercontent.com/34858915/167275374-61ef0f54-05c8-43fa-900b-55a7ed9f2642.mov

The figure below shows the complete ROS node configuration used during the autonomous driving mode.
	<p align="center">
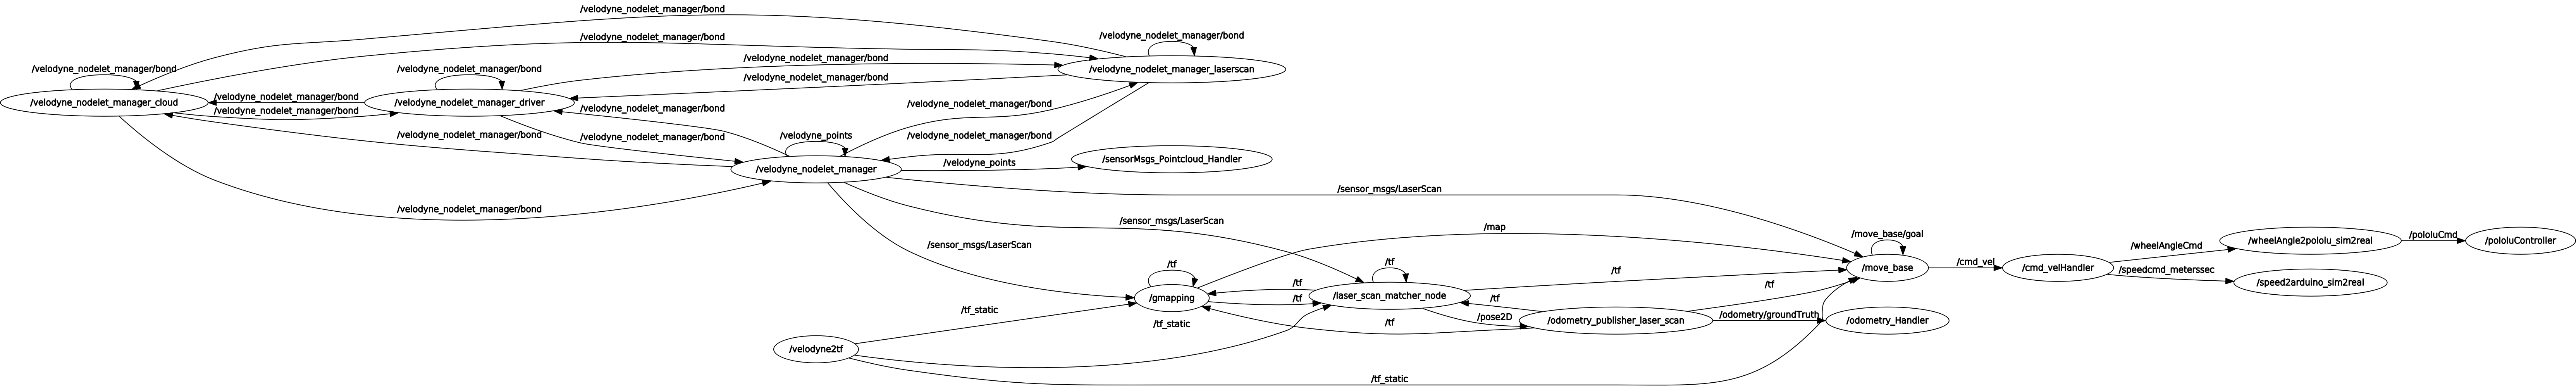
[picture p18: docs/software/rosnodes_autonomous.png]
ROS nodes used in the autonomous driving control mode with GMapping, Move_base and TEB planner.
	
	</p>

## VII.  3D Gazebo Simulation

OpenPodcar 3D Simulation (https://www.youtube.com/watch?v=Gvhzq0draLM)

### A. Installation

- Assuming: ROS Kinetic and Gazebo 7 already installed. Install instructions can be found [here](http://wiki.ros.org/kinetic/Installation/Ubuntu).

- Rosdep is also required, but is standalone since ROS Fuerte. Install instructions can be found [here](http://wiki.ros.org/rosdep).

- To install the ros package and gazebo sim locally, clone the repository and run the follow commands (directories indicated by <> need to be replaced by their actual locations):

```bash
cd <install location>/catkin_ws
catkin_make
source devel/setup.bash
cd src/podcar/models/plugins
cmake .
make
export GAZEBO_PLUGIN_PATH=$GAZEBO_PLUGIN_PATH`pwd`:
cd ..
export GAZEBO_MODEL_PATH=$GAZEBO_MODEL_PATH`pwd`:
cd ../../../
rosdep install --from-paths src --ignore-src -r -y
roslaunch podcar podcarsim.launch
```

The first run of Gazebo may take a while (e.g. 5 minutes) to load because models used need to be automatically downloaded from the remote gazebo repositories.

- Once the simulation is running, you can then launch one of two different systems to control the robot: manual joystick control or movebase control.

### B. Joystick control

If you have a USB joystick connected, open a new terminal and run,

```bash
source <install location>/catkin_ws/devel/setup.bash
roslaunch podcar joystick.launch
```

The figure below shows the complete ROS node configuration used during simulation, under manual joystick control.
	<p align="center">
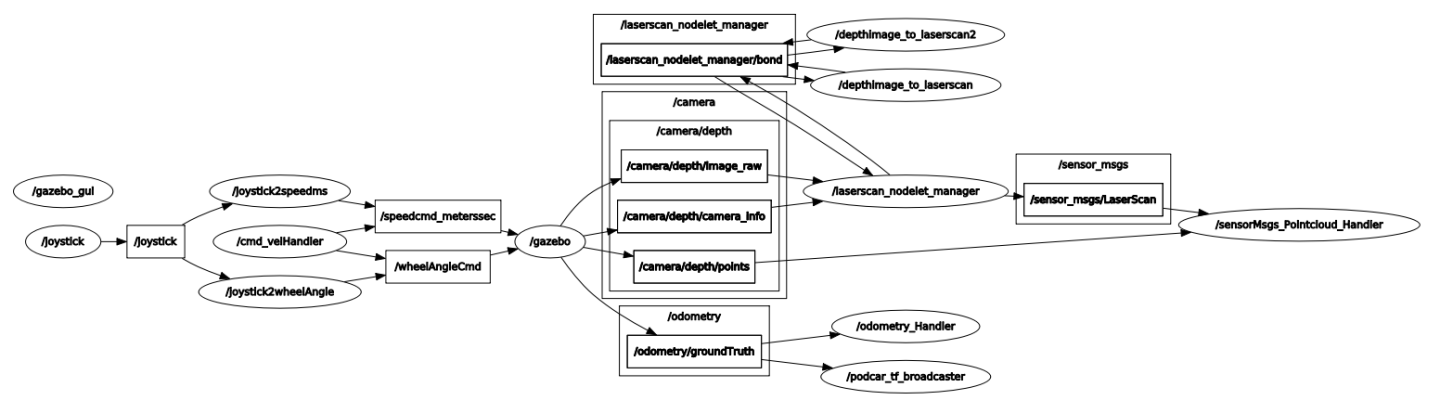
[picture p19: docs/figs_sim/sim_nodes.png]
ROS nodes used in simulation under manual joystick control
	
	</p>

### C. Move_base control

Open a new terminal and run,

```bash
source <install location>/catkin_ws/devel/setup.bash
roslaunch podcar podcarsim_moveBase.launch
```

This will present a standard movebase GUI interface in rviz, enabling you to click desired destinations to command the vehicle to drive to.

### D. 3D Environment

3D simulation environments of the University of Leeds and Lincoln campuses were created in addition to the default Gazebo environment.

The University of Lincoln campus simulation is shown in the video below.

https://user-images.githubusercontent.com/34858915/167275044-d2940f17-d5ab-4f16-85e8-6e10bda04f92.mov

## VIII.  Troubleshooting Guide

### A. Vehicle
- Vehicle beeps continuous when press DMH and rear wheels do not move
	- This is due to a safety mode preventing ignition.

	- Check: is the manual-auto switch under the rear motor on auto?

	- Check: are the batteries well charged (must be 24V or over.) ?

	- Check: is the control voltage is the dead zone ? It should be.

- Rear wheels do not move, control voltages are correct
	- Control voltages means the display on the voltmeter LED. Should be above 1.2 or below 2.2 for forward and backwards.

	- Check: main vehicle battery level, by connecting the vehicle charger and inspecting the battery charge level. Problem occurs if the battery is nearly flat.

	- Check: charger must be disconnected for rear wheels to move (safety feature).
	
- Linear Actuator
	- Diagnostic test commands can be passed to the Polulo using the commands provided in /testingTools/cmdSteer.   {\em Do not give commands outside the range 1000-2500 as they have mechanically destroyed the the vehicle.} A non-ROS test of the C API for the Pololu is provided in /testingTools/pololuTestCSerial.
	
- Speed
	- It receives commands of the form "**FA:210**" as speed commands. The test scripts /testingTools/zeroSpeed.py and /testingTools/testSpeed.py can be used to send example commands for debugging.
	
- Simlink
	- If the Simlink does not work, display all the devices by typing in terminal `ls -l /dev` to see whether your device is connected well.
	- The idVendor and idProduct can also be displayed in the commandline for each connected USB device, such as `udevadm info -q all -a -n /dev/ACM0` for the device connected at COM Port ACM0
- ROS Software:
	- It is recommended to open additional terminal(s) to check topics values and data received within ros using `rostopic echo topicName`, for example:
		- `rostopic echo /velodyne_points` displays the lidar data (a huge flow of numbers should appear in the terminal)
		- `rostopic echo /odometry/groundTruth` displays the vehicle position and orientation
	- Other useful commands include for example: `rosrun rqt_graph rqt_graph`, `rosrun tf tf_monitor`, `rosrun tf view_frames`. 

### B. Lidar
- No velodyne_points message published
	- Check: laptop must be on wired network, not wifi.

	- Check: wired network must be configured correctly, see velodyne setup docs. Maybe be interfered if wifi has been used recently.
	
	- Check connections to Velodyne box including power and Ethernet.

### C. Simulation
- AF\_NET error
	- If this is thrown by the Gazebo plugin -- it may be because Gazebo is being run standalone rather than launched as a ROS node as required.
	
- Cannot locate node i.e. you should make your Python scripts as executables in order to launch them

## IX.  How to Contribute? 

Contributions to and forks of OpenPodcar are strongly encouraged and welcomed.

Useful contributions to improve the current design could include:

- Replace the donor vehicle’s propriatory motor driver with the OSMC open source hardware motor driver

- Port the ROS code to ROS2

- Update ROS code to enable swarms of multiple podcars operating together

- Add a 3d stereo camera to the hardware and software

- Replace the body and wheels of the donor vehicle with an OSH alternative, keeping the sensors, mechatronics, and software the same.

- Interface the system into Autoware

Possible forks could include:

- Port the mechatronics and software to run on other closed source mobility scooters

- Port the mechatronics and software to run on other classes of vehicles

We would be very interested to hear about and discuss your plans, so please get in touch if interested to contribute or fork. 

Email contacts: Fanta Camara (tsfc@leeds.ac.uk / fcamara@lincoln.ac.uk) and/or Charles Fox (chfox@lincoln.ac.uk)

## X.  Cite OpenPodcar

Please cite the following paper when you use the OpenPodcar.

Plain:
```
Fanta Camara, Chris Waltham, Grey Churchill, Charles Fox. 
OpenPodcar: an Open Source Vehicle for Self-Driving Car Research. 
(under review).
```
Bibtex:
```
@Article{camara2022openpodcar,
  Title                    = {OpenPodcar: an Open Source Vehicle for Self-Driving Car Research},
  Author                   = {Fanta Camara and Chris Waltham and Grey Churchill and Charles Fox},
  Year                     = {2022},
  Journal                  = {(under review}
  }
```

## XI.  Licence 

This work is provided under GPL licence for software source code and CERN-OHL-W licence for hardware design and build instructions. 

Disclaimer: Neither the authors nor the Universities of Lincoln and Leeds are repsonsible for accidents, injuries or damage caused by this vehicle design, and by downloading, building or operating the design you agree to do so entirely at your own risk. The design is not a legal product and carries no safety certification.

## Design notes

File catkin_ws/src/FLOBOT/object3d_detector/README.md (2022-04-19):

# 3D Object Detector

This is a PCL-based ROS package for 3D object detection using 3D LiDARs.

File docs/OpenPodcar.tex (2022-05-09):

%% Hardware Metapaper Template for the Journal of Open Hardware, v.1

\documentclass[a4paper]{article}

\usepackage{lmodern}
\usepackage[T1]{fontenc}
\usepackage[utf8]{inputenc}
\usepackage{amssymb,amsmath}
\usepackage{todonotes}
\usepackage{caption, subcaption}
\usepackage{url}

\usepackage{hyperref}
\hypersetup{unicode=true,
	pdfborder={0 0 0},
	breaklinks=true}
\urlstyle{same}

\usepackage{longtable,booktabs}
\IfFileExists{parskip.sty}{%
	\usepackage{parskip}
}{% else
\setlength{\parindent}{0pt}
\setlength{\parskip}{6pt plus 2pt minus 1pt}
}
\setlength{\emergencystretch}{3em}  % prevent overfull lines
\providecommand{\tightlist}{%
	\setlength{\itemsep}{0pt}\setlength{\parskip}{0pt}}
\setcounter{secnumdepth}{0}

%% \date{}

\title{OpenPodcar: an Open Source Vehicle \\for Self-Driving Car Research}
\usepackage{authblk} 
\author[1,2]{Fanta Camara}
\author[2]{Chris Waltham}
\author[2]{\\Grey Churchill} %David has recently changed name (and gender, to they/them)
\author[1,2]{Charles Fox} 
\affil[1]{Institute for Transport Studies, University of Leeds, UK} 
\affil[2]{School of Computer Science, University of Lincoln, UK}
\renewcommand\Affilfont{\itshape\small}

\begin{document}
	\maketitle

	\begin{abstract}
		OpenPodcar is a low-cost, open source hardware and software, autonomous vehicle research platform based on an off-the-shelf, hard-canopy, mobility scooter donor vehicle. Hardware and software build instructions are provided to convert the donor vehicle into a low-cost and fully autonomous platform. The open platform consists of (a) hardware components: CAD designs, bill of materials, and build instructions; (b) Arduino, ROS and Gazebo control and simulation software files which provide standard ROS interfaces and simulation of the vehicle; and (c) higher-level ROS software implementations and configurations of standard robot autonomous planning and control, including the move\_base interface with Timed-Elastic-Band planner which enacts commands to drive the vehicle from a current to a desired pose around obstacles. The vehicle is large enough to transport a human passenger or similar load at speeds up to 15km/h, for example for use as a last-mile autonomous taxi service or to transport delivery containers similarly around a city center. It is small and safe enough to be parked in a standard research lab and be used for realistic human-vehicle interaction studies. System build cost from new components is around USD7,000 in total in 2022. OpenPodcar thus provides a good balance between real world utility, safety, cost and research convenience.
	\end{abstract}
	
	\begin{longtable}[]{@{}l@{}}
		\begin{minipage}[t]{0.97\columnwidth}\raggedright\strut

			\subsection*{Metadata Overview}\label{h.akaipbqoqfs8}
			
			Main design files: \url{https://github.com/OpenPodcar/OpenPodcar}
			
			Target group: researchers and hobbyists interested in autonomous vehicle research and robotics. 
			
			Skills required: Mechanical assembly – intermediate (drilling steel); electrical assembly – intermediate (PCB soldering); Software – easy (Linux command line).
			
			Replication: The current OpenPodcar is being used by some of the authors for human-robot interaction experiments and a second copy will be built from the documentation to improve its accuracy. The design is currently being forked for a courier-type manually-driven platform by a commercial UK vehicle manufacturer. 

			\subsection*{Keywords}\label{h.kdz351yp7g7c}
			
			{Autonomous vehicle, automation, self-driving car, mobility scooter, open source platform.}
			
			\strut\end{minipage}\tabularnewline
		\bottomrule
	\end{longtable}

	\section{(1) Overview}
	
	\subsection{Introduction}
	\label{h.pnj38xyr5dyy}
	
	Autonomous Vehicles (AVs, also known as `self-driving cars'), is a fast-moving research field in both academia and the industry. Open source software (OSS) for localisation, mapping and control of AVs is available \cite{kato2018autoware} but hardware vehicle platforms remain expensive and proprietary, making it difficult for researchers with low resources to develop algorithms or reproduce complete research systems. There is thus a need for a standard, low-cost, reproducible hardware platform, compatible with the standard open source software stack.
	
	Open source hardware (OSH) allows for more effective and accessible sharing and collaboration among researchers \cite{fisher2012open}. By combining OSH and OSS, a standard platform can be produced for use by all members of a research community, who may then reproduce each others work in full, and contribute their new research as functional system components rather than only as reports. Such platforms may evolve from research into development and real-world applications.
	
	To create an OSH platform for the autonomous vehicle research community, several requirements must be met: {\em low cost} and {\em easy to build} to enable the community to reproduce and use it; consumer levels of safety and reliability are not required, though {\em research standards of safety and reliability} are required; the system should be designed to enable {\em easy modification} so that it can be forked to operate with similar but different vehicles; the system should be physically {\em light-weight} to ease experimentation and reduce risks of damage, though large enough for {\em human transport} so that it can be used in real-world applications and in research requiring realistic interactions with other human road users \cite{camara2021evaluating, delucia2013effects}.
	
	\subsection{Related Systems}
	\label{related_systems}
	
	SMART \cite{pendleton2015autonomous} is a design to modify an existing donor golf cart vehicle for automation research, this is of a similar size and power to OpenPodcar. Similarly, iCab (Intelligent Campus Automobile) \cite{gomez2016ros} is research golf car with a ROS (Robot Operating System)-based architecture and that has been tested with Timed-Elastic Band planner \cite{marin-plaza2018global}. However, these vehicle designs are not open source hardware.
	
	Complete and built mechanical OSH designs for on-road, person-carrying cars exist, including PixBot \cite{pixmovingpixbot} and Tabby EVO \cite{openmotorstabby}. Building these full size cars is a large task for experts and may require dangerous processes such as welding, purchase of expensive components, and considerable storage space. OpenPodcar is based on a proprietary but commodity mobility scooter which is cheaper and easier to convert than performing these builds. 
	
	Several OSH RC-scale cars have been completed and built such as F1Tenth \cite{f1tenth}, AutoRally \cite{goldfain2019autorally}, BARC \cite{gonzales2018planning}, MIT Racecar \cite{mit}, MuSHR \cite{mushr}, \cite{nakamoto2019development}, and \cite{vincke2021open}. These platforms are not large enough to drive on public roads or to transport people or goods like OpenPodcar. Open Source Ecology (OSE) \cite{jakubowski2003open} is an ambitious programme of projects which ultimately aims to develop fully OSH vehicles including a car and tractor. OSE is optimised for reliability and for users in developing countries so it uses hydraulic power rather than electric as used in OpenPodcar. But its vehicle designs are not yet complete.
	
	Autoware \cite{kato2018autoware} is a heavyweight open source software project to construct a full ROS-based automation stack for on-road cars. Apollo \cite{apolloautoapollo} is an open source self-driving software stack and an open hardware interface which may be implemented on vehicles, as done in \cite{kessler2019bridging}. These systems could be software interfaced to run with OpenPodcar. 
	
	Some AV research can be done in simulation without the need for hardware, hence open source simulation platforms are widely available such as SUMMIT \cite{cai2020summit}, Gym-Duckietown \cite{chevalier-boisvert2018duckietown}, CARLA \cite{dosovitskiy2017carla}, DEEPDRIVE \cite{quiterdeepdrive}, LGSVL Simulator \cite{rong2020lgsvl}, AirSim\cite{shah2017airsim}, and FLOW \cite{wu2017flow}. The USA state of Georgia provides a level 3 open-source autonomous vehicle based on a Ford-Edge\cite{peachtreecuriosity}, which can be used {\em gratis} in their Peachtree Corners' Curiosity Lab smart city environment by researchers needing a vehicle but not wanting to build or buy one.
	
	\section{(2) Overall Implementation and Design}\label{h.1u7vph94gfbt}
	
	\subsection{Donor vehicle}
	
	A Pihsiang TE-889XLSN hard-canopy scooter (branded in UK as Shoprider Traverso, \cite{shoprider2016shoprider}) is used as a donor vehicle. It is an Ackermann-steered \cite{milliken1995race}, hard-canopy, electric mobility scooter. It is powered by two 12V batteries connected in series to provide 24V operating voltage and containing 75Ah. In its standard configuration, its steering is controlled by a human-operated loop handle bar. The speed and braking systems are both powered by an electric motor and an electric brake via the trans-axle assembly, controlled by an AC2 digital controller receiving different voltage signals to drive forward or brake. The manual speeding and braking systems are controlled by three buttons connected in series on the handle bar. A toggle switch in parallel with a resistor (10k$\Omega$) selects  speed mode from high (max 8mph) or low (max 4mph); a speed dial knob via a variable resistor (20k$\Omega$) sets a maximum limit speed within the mode. A throttle lever connected with a 5k$\Omega$ potentiometer is used to select the speed within the mode and limit.
	
	\subsection{Mechanical Modification for Steering}
	
	To automate steering, a linear actuator (Gimson GLA750-P 12V DC) with position feedback is mounted between an anchor on the underside of the chassis and the car's front axle via bearings.  This actuator has a 8mm/s full load (750N) speed and 250mm stroke length (installation length is 390mm). To access the underside of the vehicle, two axle stands are used as shown in Fig. \ref{fig:axelStands}. There is an existing hole in the right front wheel axle. The linear actuator is mounted via a rear hole to the left side of the front chassis and connected through the front hole of the actuator with the hole in the car's right front wheel axle via bearings as shown in Figs. \ref{fig:actuatorMounted} and \ref{fig:steering}.

	\begin{figure}
		\centering
		\begin{subfigure}{0.45\textwidth}
			\centering
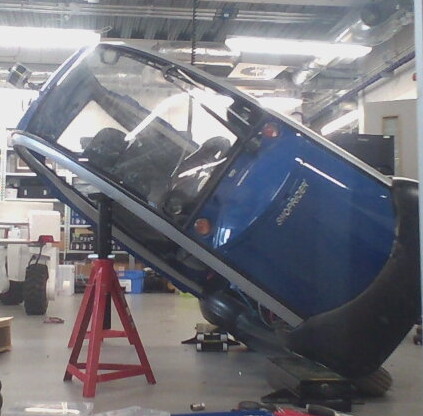
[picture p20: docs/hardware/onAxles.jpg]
			
			\caption{Tilting the vehicle using two axle stands, to enable access to the underside. (Note also lidar mounted to roof.)}
			\label{fig:axelStands}
		\end{subfigure}	
		\quad
		\begin{subfigure}{0.45\textwidth}
			\centering
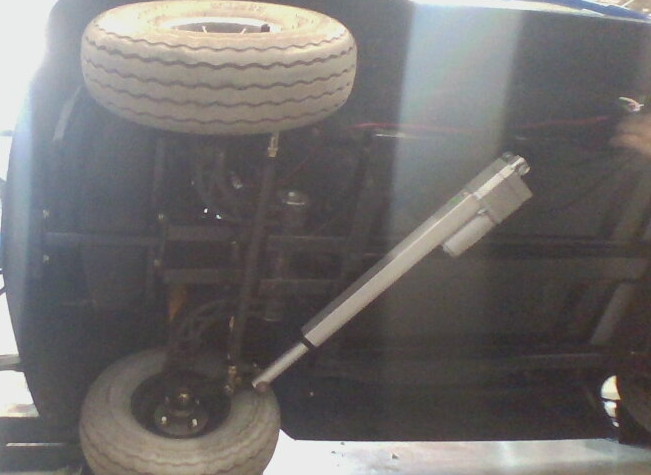
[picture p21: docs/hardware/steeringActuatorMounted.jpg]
			
			\caption{Underside with linear actuator added for steering.}
			\label{fig:actuatorMounted}
		\end{subfigure}
		\caption{Vehicle mechanical modification}
	\end{figure}

	\begin{figure}[h]
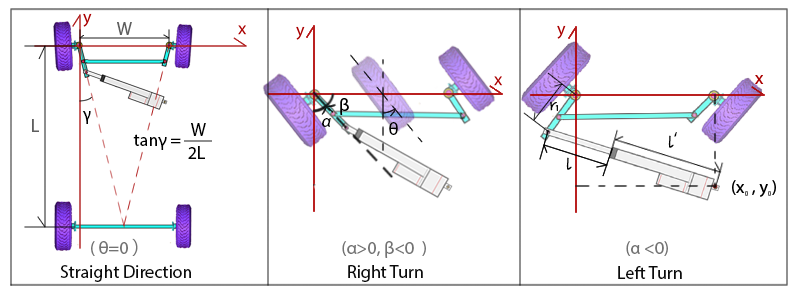
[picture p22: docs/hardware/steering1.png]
		
		\caption{Underside view of front wheels' steering relationship including geometric coefficients}
		\label{fig:steering}
	\end{figure}

	\subsection{Electronics}
	
	\begin{figure*}[h]
		
		\caption{Circuit diagram for electronic modifications.}
		\label{fig:circuitDiagram}
	\end{figure*}

	The new vehicle electronics, which various different voltage power supplies (cf. Fig. \ref{fig:circuitDiagram}), are packaged on a single new PCB (Printed Circuit Board), as shown in Figs.~\ref{fig:pcb_design} and \ref{fig:pcb_assembled}. This is convenient as it reduces the number of small wires between the components by having them directly drawn on the board, and packages them together.
	
	As an OSH design, the PCB hosts several daughter PCBs, mounted using headers. The physical structure of the large PCB comprised of these smaller PCBs reflects the OSH design itself. There are two DC-DC Buck converters with an XL4016 regulator, an Arduino Uno, an MCP4725 DAC (Digital-Analog Converter), a Pololu Jrk 21v3 motor controller with position feedback for the linear actuator, two resistors (10k$\Omega$ and 100k$\Omega$) for the potential divider and two terminal blocks. 3D-printed parts support the mounting of the LCD and the 3D lidar to the board. A 3D printed enclosure mounts and protects the PCB board, as shown in Fig.~\ref{fig:pcb_enclosure}.
	
	\begin{figure}
		\centering
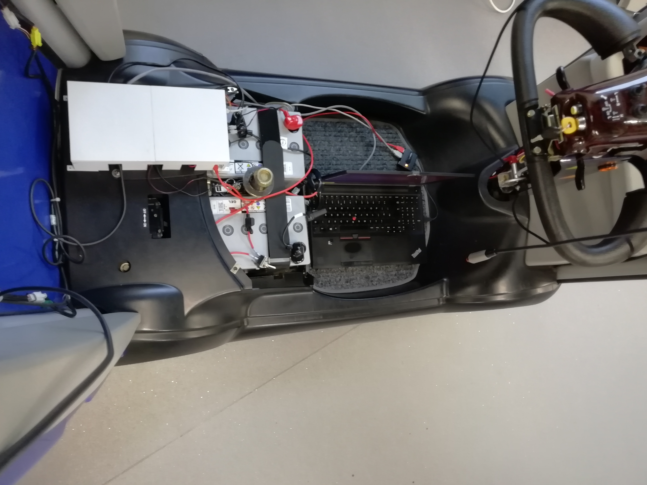
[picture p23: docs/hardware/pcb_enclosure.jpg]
		
		\caption{PCB enclosure mounted on the vehicle (top left, white box).}
		\label{fig:pcb_enclosure}
	\end{figure}
	
	\begin{figure}
		\centering
		\begin{subfigure}{0.45\textwidth}
			\centering
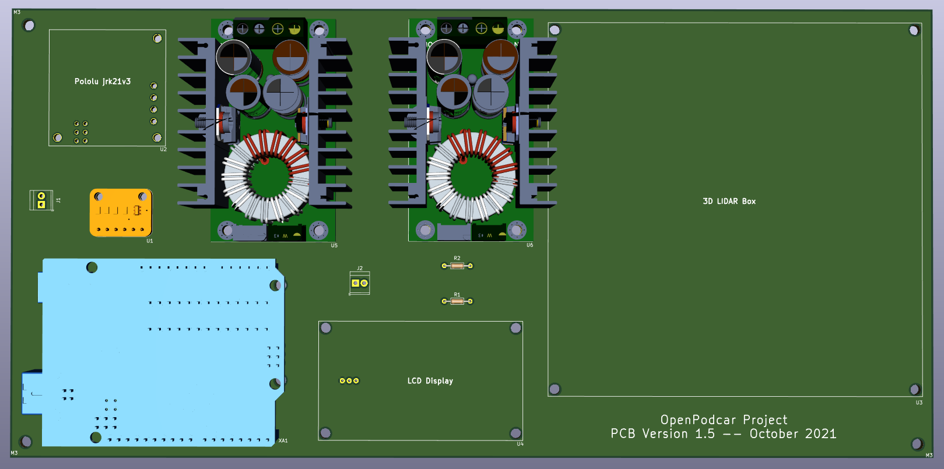
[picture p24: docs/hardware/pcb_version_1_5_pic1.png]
			
			\caption{PCB Design.}
			\label{fig:pcb_design}		
		\end{subfigure}
		\quad
		\begin{subfigure}{0.45\textwidth}
			\centering
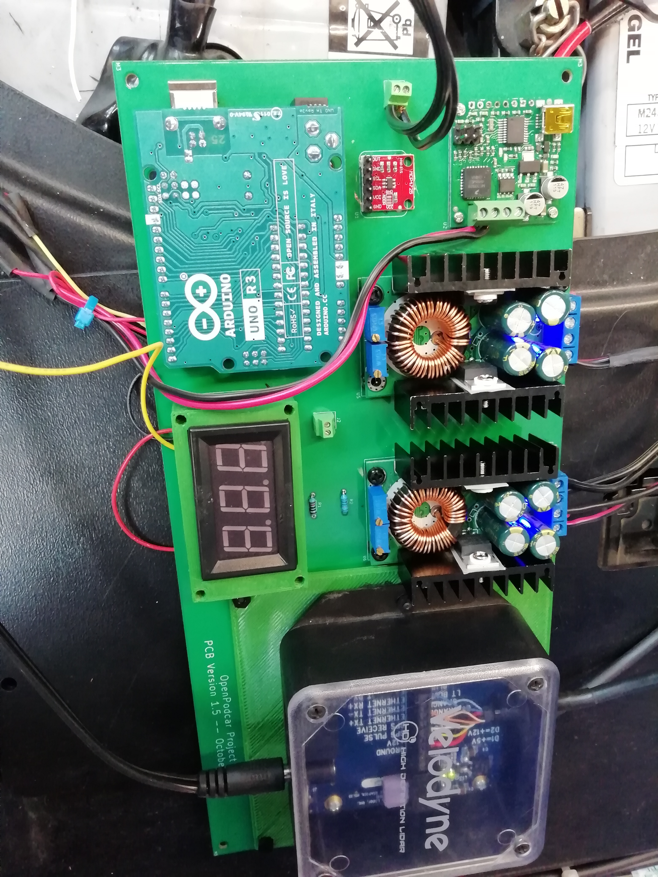
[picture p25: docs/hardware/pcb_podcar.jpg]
			
			\caption{PCB assembly currently used.}
			\label{fig:pcb_assembled}
		\end{subfigure}	
		\caption{Electronics with PCB board design and assembly}
	\end{figure}

	\subsection{Steering Automation System}
	
	The front wheels are steered by a Pololu Jrk 21v3 PID controller-driver, which takes serial port desired positions as input. It also takes feedback position information as an analog voltage from the linear actuator as an input. It outputs analog high-power voltages to the linear actuator. A gratis, closed-source, Windows program from Pololu is required once, at build time, to set the PID parameters for the linear actuator. 
	
	The relationship between the required central turning angle $\theta$ of the pair of front wheels and extending length $l$ of linear actuator as in Fig. \ref{fig:steering} is given by,    
	\begin{gather}
	\theta = \alpha - \arctan(\frac{W}{2H}) \\
	% update W and H in figure. W is the width between two front wheels and H is the distance between front wheel and rear wheel.
	\beta = \alpha -\frac{\pi}{2}\\
	x = r_1 \cos(\beta) \\
	y = r_1 \sin(\beta) \\
	l = \sqrt{(x_0-x)^2 + (y_0-y)^2} - L + l_0    
	\end{gather}    
	where $r_1$, $x_0$, $y_0$, $W$, $H$ and $L$ are the geometric coefficients shown in Fig.1. Among them, the value of $y_0$ is negative. $l_0$ is the initial value of the linear actuator position feedback. Table \ref{tab:linear_actuator} specifies the acceptable serial port commands for the linear actuator. Sending commands outside this range may mechanically destroy the system.  
	\begin{table}
		\begin{center}
			\caption{Linear actuator acceptable command ranges.}
			\label{tab:linear_actuator}
			\begin{tabular}{ c c }
				\hline
				FA:cmd     &  Effect \\
				\hline
				2500    &    turn max right i.e $\sim$ -45 deg \\
				1900    &    center wheels i.e $\sim$ 0 deg \\ 
				1000    &    turn max left i.e $\sim$ +45 deg \\
				\hline\\
			\end{tabular}
		\end{center}   
	\end{table}

	\subsection{Speed Controller Automation System}
	
	An Arduino UNO \cite{oxer2011practical} is used to send electric signals to the vehicle's motor controller in place of the donor vehicle’s paddle controller’s potentiometer. An Adafruit MCP4725 DAC is connected to the Arduino as in Fig. \ref{fig:circuitDiagram}, and is used to send clean analog speed command voltages to the donor vehicle’s internal controller.
	
	Arduino firmware source, and upload instructions, are supplied in the repository. When uploaded to the Arduino (using the standard Arduino IDE running on the laptop), the firmware provides a simple serial port API running at 112,000 baud. It receives ASCII commands of the form `FA:210' as speed commands. Table \ref{tab:speed_commands} summarises the range of speed commands and their corresponding output voltages. 
	
	\begin{table}
		\begin{center}
			\caption{Speed commands and their corresponding output voltages.}
			\label{tab:speed_commands}
			\begin{tabular}{ l c c }
				\hline
				Command   &    Voltage            &  Effect \\
				\hline
				FA:0      &    0                  & very fast reverse  \\
				FA:80     &    $\sim 0.9$         & fast reverse (ROS limit) \\
				FA:132    &   $\sim 1.5$          & slowest reverse motion  \\
				&                       & dead zone - allows ignition \\
				FA:170    &    1.9                & stop - zero/home position \\
				FA:201    &    $\sim 2.3$         & slowest forward motion \\
				FA:240    &    $\sim 2.7$         & fast forward (ROS limit) \\
				FA:255    &    $\sim 3.0$         & very fast forward \\
				\hline\\
			\end{tabular}
		\end{center}    
	\end{table}
	
	To start the ignition, the car safety system requires the control voltage to be in the dead range. A problem is that this doesn’t correspond precisely to any fixed speed bytes, due to floating USB power level issues.  But if we pick a number solidly in the center of the dead zone, such as 164, this will work for most USB supplies. (i.e. when the vehicle’s battery is flatter, the voltages provided to USB power by it are lower. For example, we might send 164 and get 1.9V instead of the usual 2.26V.) This may result in the vehicle not starting and producing an audible warning beep instead.
	
	Also due to floating voltages from the battery, the Arduino typically receives a lower power e.g. 4.9V instead of its ideal 5V, which gets divided by the DAC value in some calculations. 
	
	To deal with these instabilities, a potential divider is added to the battery to monitor its  voltage and compensate the podcar control accordingly, as in Fig. \ref{fig:potential_divider}. A ``BV'' command is provided in the Arduino serial protocol which allows callers to request this current battery voltage. This can then be used by higher-level (Python) systems to decide what speed bytes to sent, including compensating for the floating dead zone.
	
	\begin{figure}
		\centering
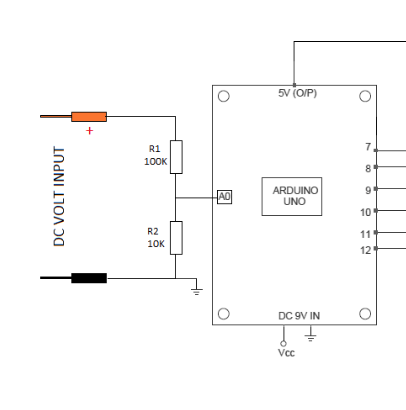
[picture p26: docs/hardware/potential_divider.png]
		
		\caption{Potential divider linked to the battery}
		\label{fig:potential_divider}
	\end{figure}
	
	\subsection{Software Interface (ROS)}
	
	A ROS interface to and from the physical vehicle is provided as described below. ROS is an open source operating system for robots based on a publish-subscribe pattern \cite{quigley2009ros}, which is the robotics community’s standard interface. The ROS core and software all run on a consumer laptop computer mounted on-board the vehicle, and that could be powered from a DCDC converter from the vehicle battery, running Xubuntu 16.04 (Xenial) and ROS Kinetic. 
	
	The system expects to hear two incoming ROS control messages: /speedcmd\_meterssec and /wheelAngleCmd, which contain single floats representing the desired speed in meters per second, and the desired front wheel orientation in radians respectively. These two messages are received by ROS nodes speedm2arduino and wheelAngle2Pololu, which are ROS drivers for the Arduino speed controller and the Polulo steering controller respectively. Converters from a standard ROS USB joystick driver node to the speed and angle command interface messages are provided, by joystick2speedms and joystick2wheelAngle. These use the $y$ axis of a joystick for speed and $x$ for steering.
	
	\subsection{3D Lidar Sensor}
	A Velodyne VLP-16 lidar sensor is mounted on the vehicle roof using a Manfrotto Black Digi Table Tripod 709B. It is mounted at a 10 degree tilt downwards (to allow pedestrians to be most clearly seen in the 16 scan lines). The lidar has a ROS driver. 
	
	\subsection{High-Level Automation Software}
	
	Fig. \ref{fig:rosnode_autonomous} shows an overview of the ROS components used in high level automation, including localisation and mapping, path planning and control, and pedestrian tracking as discussed in the following sections.
	\begin{figure}[h]
		
		\caption{ROS nodes used in the autonomous driving mode.}
		\label{fig:rosnode_autonomous}
	\end{figure}
	
	\subsubsection{Localisation and Mapping System}
	
	Simultaneous Localisation and Mapping (SLAM) \cite{thrun2002probabilistic} is the robotic task of inferring the robot’s location at the same time as building a map of its environment, which is a classic `chicken and egg’ problem as the two subtasks depend on one another. Solving SLAM is an NP-hard problem but many standard approximations exist. GMapping \cite{yuen2017improved} is a ROS implementation of a Rao-Blackwellized Particle Filter (RBPF) in which ``each particle carries an individual map of the environment''. The information carried by each particle overlaps, and an estimation of a map can be built based on these relationships. As the robot moves around the environment, these estimations are stored, and when a ‘feedback loop’ is closed, the estimations cascade into a portion of the completed map. These maps take the form of 2D occupancy grids, and can be used later by the navigation stack to plan paths around the environment.  To provide reliable odometry data for GMapping, ROS laser\_scan\_matcher package is used  as a stand-alone odometry estimator that matches consecutive laserscans.

	\subsubsection{Path Planning and Control}
	
	Path planning is the autonomous selection of an entire desired trajectory for a robot to get from a current pose to a desired pose. Path control (or path following) is then the real-time process of executing a path plan by interactively monitoring the robot’s state and sending commands to motors, to make the actualized path close to the desired path. The OpenPodcar software includes path planning and control with the standard ROS tool move\_base and Timed Elastic Band (TEB) \cite{rosmann2013efficient} plugin. These tools implement the requirement geometry of Dubins paths \cite{dubins1957curves} and Ackermann steering. The values for parameters such as minimum turning radius have been calculated from the technical specifications of the base vehicle \cite{shoprider2016shoprider}.
	
	\subsubsection{Pedestrian Detection and Tracking}
	
	A pedestrian detector and tracker ROS package are included in the system.  The lidar-based detections are classified by a SVM (Support Vector Machine) classifier, then a Bayesian multi-target tracker is used to track pedestrians over time. These modules re-use OSS from the EU FLOBOT project \cite{yan2020robot}, merged into the repository.

	\subsection{Simulation}
	
	\begin{figure}
		\centering
		\begin{subfigure}{0.45\textwidth}
			\centering
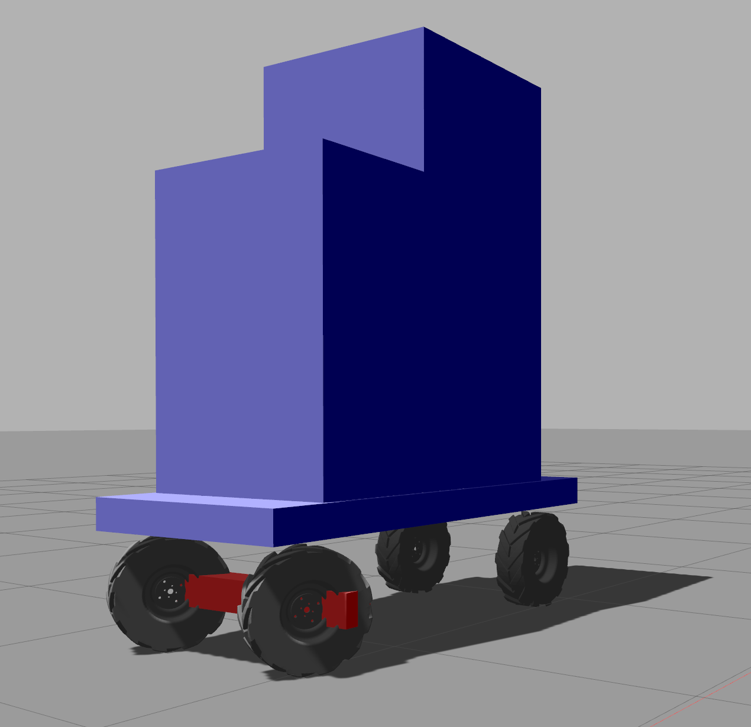
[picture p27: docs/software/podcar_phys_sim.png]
			
			\caption{Physical simulation of vehicle.}
			\label{fig:physSim}
		\end{subfigure}	
		\quad
		\begin{subfigure}{0.45\textwidth}
			\centering
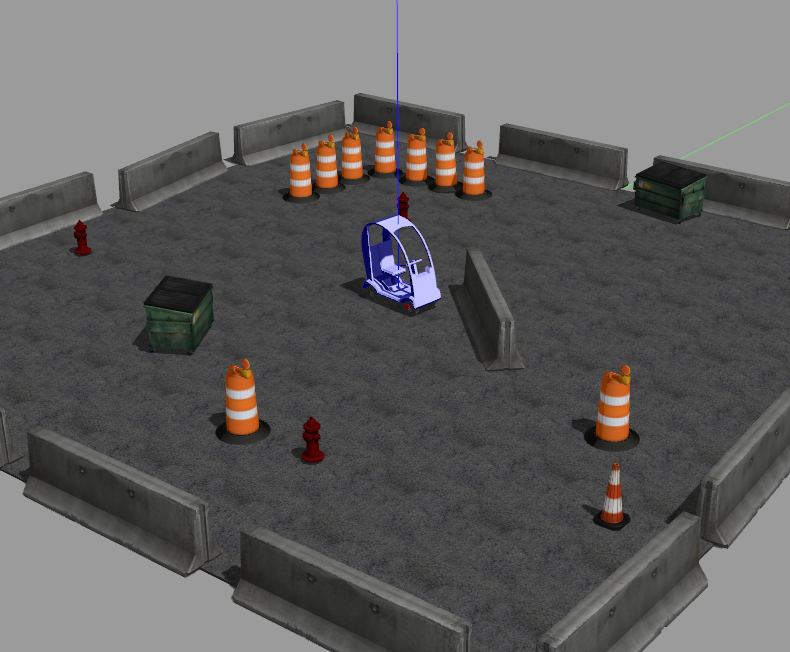
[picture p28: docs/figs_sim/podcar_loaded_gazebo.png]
			
			\caption{Default Gazebo simulation world}
			\label{fig:sim_world}
		\end{subfigure}
		\caption{OpenPodcar 3D simulation}
	\end{figure}
	
	\begin{figure}
		\centering
		\begin{subfigure}{0.45\textwidth}
			\centering
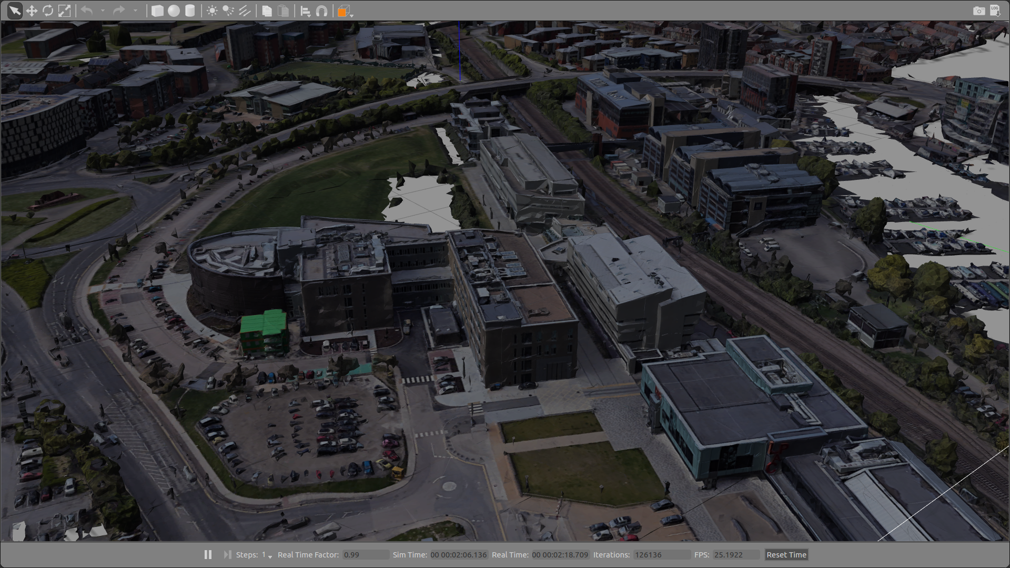
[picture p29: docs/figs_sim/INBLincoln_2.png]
			
			\caption{University of Lincoln 3D world}
			\label{fig:INB_world}
		\end{subfigure}	
		\quad
		\begin{subfigure}{0.45\textwidth}
			\centering
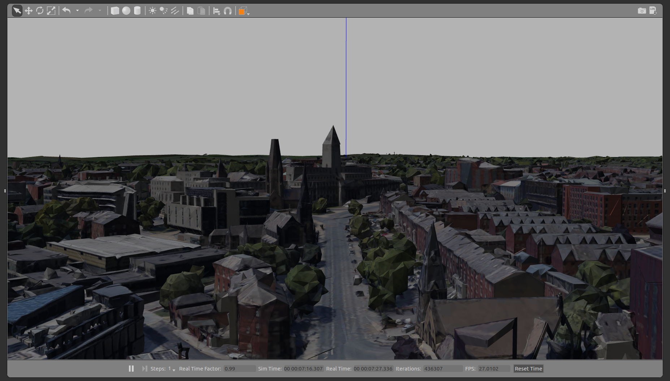
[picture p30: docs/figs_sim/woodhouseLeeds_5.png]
			
			\caption{University of Leeds 3D world}
			\label{fig:Leeds_world}
		\end{subfigure}	
		\caption{OpenPodcar additional Gazebo 3D simulation worlds}
		\label{fig:gazebo_new_worlds}
	\end{figure}
	
	\begin{figure}
		\centering
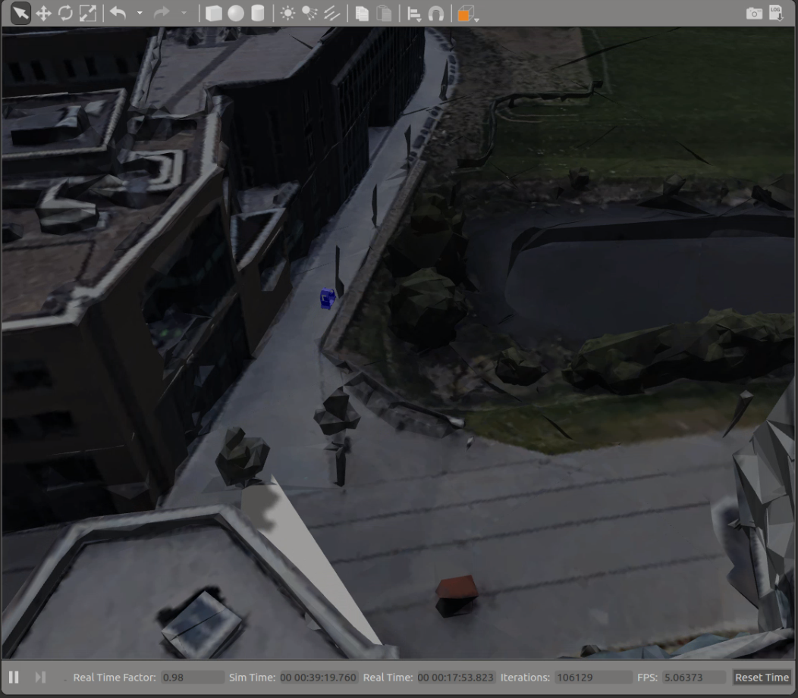
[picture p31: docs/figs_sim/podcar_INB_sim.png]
		
		\caption{OpenPodcar in Lincoln world}
		\label{fig:sim_INB_world}
	\end{figure}
	
	A physical simulation of the vehicle is provided for use in Gazebo 7 \cite{koenig2004design} under ROS Kinetic and Ubuntu 16.04 (Xenial). The simulation implements the same ROS interface as the physical vehicle system to enable plug and play inter-operability between them. The physics model is based on a simplified vehicle geometry with two large cuboids containing the vehicles’ mass, as shown in Fig. \ref{fig:physSim}. Wheel geometry, friction, and motor driver parameters were measured from the physical vehicle. A detailed graphical mesh model of the vehicle is provided for display, rather than physical simulation, purposes. The main difference with the real vehicle is that the effects of the linear actuator are represented by a tracking rod, where is mounted the Kinect sensor used in place of the lidar, as found in Fig. \ref{fig:sim_world}.
	
	A basic 3D world containing the podcar and various test objects from Gazebo libraries is provided by default as shown in Fig. \ref{fig:sim_world}. Fig. \ref{fig:sim_nodes} shows the complete ROS node configuration used during simulation, under manual joystick control. Moreover, the open source Blender 3D add-on, called MapsModelsImporter \cite{michelmaps}, was used to create further 3D worlds representative of the University of Lincoln, the testing area for the OpenPodcar, and the University of Leeds campuses, shown in Fig.\ref{fig:gazebo_new_worlds}. Fig.~\ref{fig:sim_INB_world} shows the OpenPodcar in Lincoln campus environment.
	
	\begin{figure}[h]
		
		\caption{ROS nodes used in simulated,  manual joystick control mode.}
		\label{fig:sim_nodes}
	\end{figure}
	
	\section{(3) Quality Control}\label{h.f8237gmzmwc6}
	
	\subsection{Safety}\label{h.v60aduckfisj}
	
	Autonomous vehicles can present a significant hazard to humans and to the environment in which they operate. Damage to surroundings and possible injury to operators and bystanders could result from inappropriate use or malfunction. A particular risk arises from the speed controller on the donor vehicle being of 'wigwag' style, as is common in mobility scooters. This means it is an analog signal in the range 0-5V, including a dead zone around 2.5V corresponding to no motion. Above the dead zone and up to 5V are forward speed control commands of increasing speeds, below the dead zone to 0V are reverse control commands of increasing speeds. Wigwag control is  potentially dangerous because a 0V signal might appear due to component failure rather than as a desired max-speed reverse command. Also, if the vehicle batteries run low, the scaling of this signal may be altered resulting in the dead zone position floating and leading to further undesired motion. The following layered safey systems are included to fully mitigate these risks:
	
	\paragraph{Fusing} As shown in Fig.~\ref{fig:circuitDiagram}, a 10A fuse is inserted between the vehicle's original 24V battery and the switch to the new electronics. This is in addition to original fusing and other safety features provided by the donor vehicle, which all remain in tact. 
	
	\paragraph{Dead Man's Handle} It is essential that a suitable emergency stop system is implemented in all autonomous vehicles. Given the research nature of the OpenPodcar, a safety mechanism which stops the vehicle under fault conditions is an especially important part of the design. A wired dead-man's handle (DMH) is included which is required to be pressed by a human experimenter at all times, in order for a hardware relay to actively continue to supply power from the vehicle’s batteries to all other systems. The relay connects to the donor vehicle's keyed ignition switch and will naturally cut out if these signals are absent for any reason, including failures in the safety systems themselves. A photograph of the installed system is shown in Fig. \ref{fig:relay}.
	
	\begin{figure}
		\centering
		
		\caption{Steering console showing the newly added relay (with lit LED)}
		\label{fig:relay}
	\end{figure}
	
	\paragraph{Heartbeat Signal} The serial protocol linking the Arduino to ROS includes a heartbeat signal, in which the Arduino code will shut down the motors unless a correctly formatted and timestamped serial command is received within 0.1 seconds. This requires ROS code to actively check and confirm its own status and to send positive confirmation, for example if ROS or Linux go down then this heartbeat will cut off.
	
	\paragraph{Steering Control System Limiter} Limitations are placed on the steering controller for the linear actuator commands, to only allow the vehicle to accept and execute input values within the range that will keep the mechanical mounting safe.

	\subsection{ General Testing}\label{h.wbekh9ay82yu}
	
	A series of sub-component (e.g. Pololu, DAC) acceptance tests, component (e.g. PCB, lidar) hardware unit tests, and system integration tests are defined and included as formal, non-optional steps in the build instructions.  The structure of the tests is designed to enable build problems to be immediately localised, so that passing one test means that a failure of the next one must be due to build steps that have occurred between them. Below is a summary of these tests.
	
	At component level, an external power supply, a multi-meter, a clamp meter and a breadboard with some wires are frequently used to recreate smaller electronic circuits in order to check the voltages, currents and the correct functioning of each component during the build. For instance, a circuit with an external power supplying 5V to the Arduino connected to the DAC is temporally created to test the Arduino code and its communication with the DAC.  Similarly, another test circuit is created with an external power supplying 12V to the Pololu connected to the linear actuator to send direct commands via the Windows program used to fix the PID parameters. These hardware unit tests are essential to the success of components' integration to the vehicle and make things easier later. 
	
	At system integration level, udev rules are used to facilitate testing with the creation of simlinks, i.e. dynamic assignments for the laptop USB ports connected to the Arduino and the Pololu, using their respective product and vendor IDs. This helps in being able to physically interchange the USB ports without having any impact at the software level. For the speed control, the vehicle wheels are lifted from the ground using jacks to stop them from driving off. This technique helps to test and fix the Arduino and ROS speed control code whilst staying in the same place. Vehicle steering is first tested using the Windows app that allows direct commands to be directly sent to the linear actuator. This helps verify and fix the linear actuator mounting as desired. Similarly, using Pololu's C++ API, direct commands are sent from a terminal to the linear actuator, but this time for testing at the software level. 
	
	Driving tests are initially performed in the manual joystick control mode in order to ensure that both hardware and software stack work well together. In particular, the LCD on the PCB board helps with checking in real-time the voltage received for each speed command and the LEDs colors displayed on the Pololu also give useful indications about the steering control. 
	
	The autonomous driving tests with move\_base and TEB are performed with the vehicle speed controls dial know set to `5', corresponding to about $0.2$m/s. This relatively low speed is chosen because these tests may be performed in a shared and cluttered research lab around people. Also, a large inflation distance is set in the planner to prevent the vehicle from close contacts with both static and dynamic obstacles. At first, simple and short goals are sent to move\_base such as ``drive one meter forward and keep your current orientation'' or ``drive three meters forward and keep your current orientation''. Once the vehicle is able to execute and reach these simple goals, more complex goal commands are sent. Once a goal is reached, it is possible to resend immediately another goal without having to turn off the system, which is very convenient for example when one wants to ask the vehicle to return to its starting position or go somewhere else. 
	
	Setting a very high accuracy for goals such as $1$mm and $0.01$rad is achievable on the vehicle and is tested for short drives in the lab. However, in these cases, the short drives may end up taking a lot of time, for example it can take up to three minutes to simply reach a one meter forward goal. This is due to the planner's oscillating behaviour around the goal. To fix this, more tolerance should be given for the goal accuracy, for example, 150mm and 0.15rad give an acceptable vehicle behaviour. During these driving tests, ROS topics and RViz (ROS visualization tool) are particularly monitored to get informed about the vehicle behaviour in real-time. 
	
	OpenPodcar was developed, and our own build was heavily tested, between March 2018 and March 2022. With its first automated test drives taking place since summer 2018 and an estimated 100km or more driven to date, the vehicle design has thus proven robust enough for autonomous vehicle research. 

	\section{(4) Application}\label{h.f78bi3oom0mu}
	
	\subsection{Use Cases}
	
	\subsubsection{Self-Driving  Research}\label{h.4q5g9edishy3}
	
	\begin{figure}
		\centering
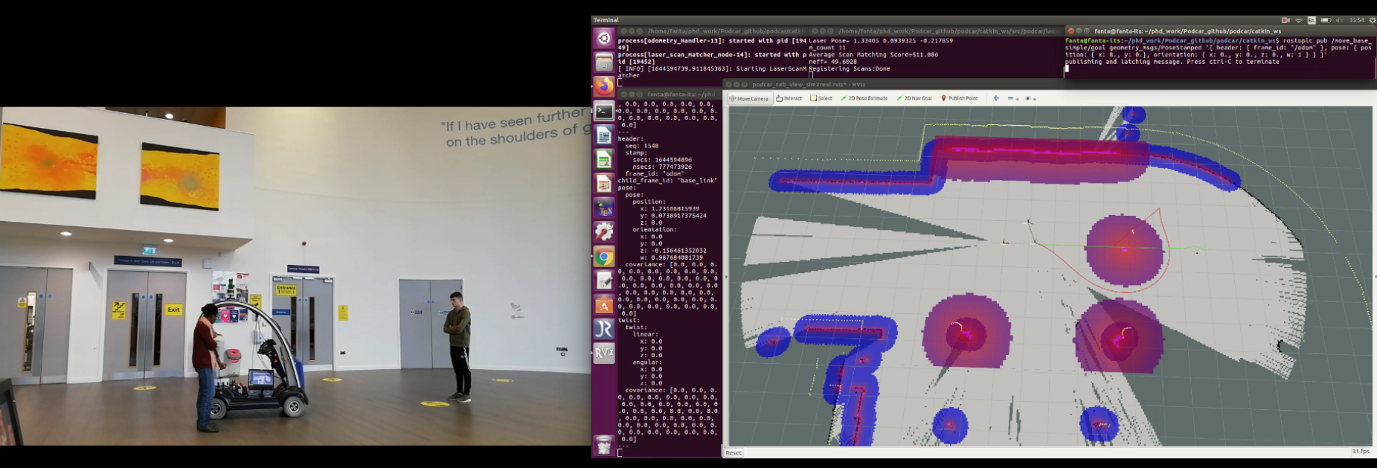
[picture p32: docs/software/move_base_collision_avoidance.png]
		
		\caption{OpenPodcar test drive with GMapping SLAM, ROS move\_base with TEB planner and obstacle avoidance.}
		\label{fig:testDrive_gmapping}
	\end{figure}
	
	Many AV researchers cannot currently afford the acquisition of a self-driving hardware platform for their work. The OpenPodcar is primarily designed for this purpose, as a low-cost and an all-in-one, software and hardware platform for researchers and hobbyists. Thus, giving them not only the opportunity to reproduce, develop and test algorithms on a physical hardware platform but also to extend its capabilities with new features. 
	
	The \nameref{related_systems} section found that there are many open source software stacks without related open hardware platforms.  OpenPodcar thus fills this gap, offering the opportunity not only to deploy Autoware or other types of AV software but also to extend the hardware capabilities to the point where OpenPodcar could become a standard test bed for the AV research community. For example, this platform could be useful to test different SLAM and planning algorithms, parallel and valet parking methods. The objective being that both hardware and software can be tested regularly in real-world conditions and contribute towards the deployment of AVs. The OpenPodcar can avoid both static and dynamic obstacle using the integrated feature in move\_base and TEB planner. Fig. \ref{fig:testDrive_gmapping} shows the OpenPodcar test drive with GMapping, move\_base and TEB planner in action when it encounters an obstacle on its path.     
	
	\begin{figure}
		\centering
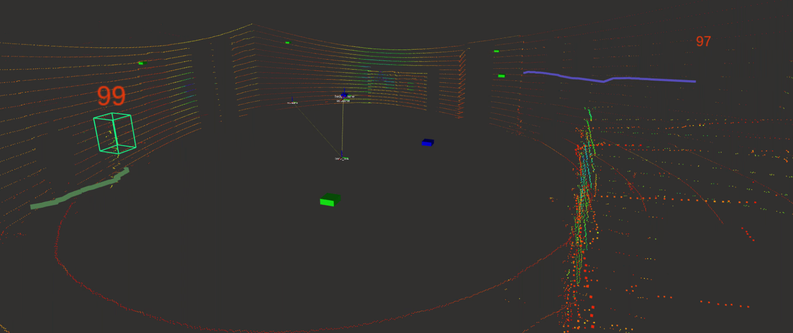
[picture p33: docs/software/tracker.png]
		
		\caption{Pedestrian detection and tracking output from RViz.}
		\label{fig:detection_tracking}
	\end{figure}
	
	\subsubsection{Human-Robot Interaction Research}
	
	Understanding human behaviour and interaction strategies are of upmost importance nowadays for autonomous systems. There is a general growing interest from the robotics and autonomous vehicle research communities to tackle the numerous challenges posed by human interactions. Social robots as well as autonomous vehicles need better models of human behaviour \cite{camara2020pedestrian, camara2020pedestriana}. Some of the authors (FC and CF) are particularly interested in improving autonomous vehicles' decision-making using a game theoretic approach for road-crossing scenarios \cite{fox2018when}. Several empirical studies e.g. \cite{camara2018towards, camara2020continuous, camara2018empirical}, were performed in highly safe lab environments and found that human participants were not interacting realistically with the other agent. A similar experiment performed in a VR environment showed a more realistic behaviour from the participants \cite{camara2021evaluating, camara2019towards}. An additional model of human proxemics (i.e., interpersonal distances) has been developed and is being combined with the game theory model \cite{camara2020space, camaraextending}. In future work, the OpenPodcar will be used to extend these human experiments using a real physical platform and demonstrate the operation of game theoretic behaviour on a autonomous vehicle for the first time. The pedestrian detection and tracking feature will be particularly useful for this task, since the AV needs to track the pedestrian in order to make a decision. Fig. \ref{fig:detection_tracking} shows an example output of the pedestrian detection and tracking integrated in the OpenPodcar.

	\subsubsection{Practical Transportation}
	
	\begin{figure}
		\centering
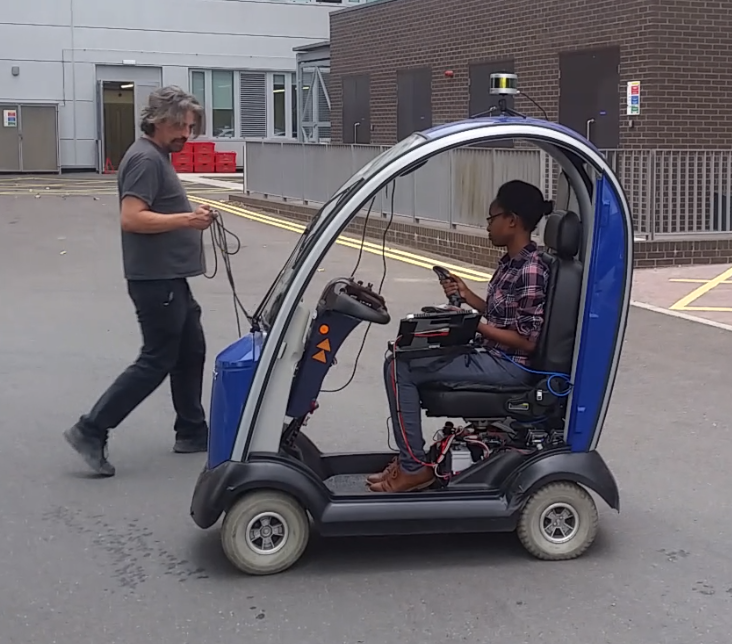
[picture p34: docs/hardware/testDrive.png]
		
		\caption{OpenPodcar test drive in remote control mode.}
		\label{fig:testDrive}
	\end{figure}
	
	OpenPodcar can carry at least 76kg of payload, such as a person or parcels, making it potentially useful for real-world as well as research applications.
	
	Last mile delivery of parcels could replace human workers for e-commerce deliveries. Urban center retail environments may also be improved by replacing the last mile of supply {\em to} retail outlets. Instead of driving to a shop to deliver goods, heavy goods vehicles could instead park a mile outside the urban center and transfer the goods to OpenPodcar or similar electric autonomous vehicles to take to the shop, reducing local pollution. The Covid-19 pandemic emphasised a specific need for {\em autonomous} last-mile delivery: to reduce the need for human contact and potential disease transmission at the point of delivery.
	
	OpenPodcar is able to transport a human passenger, as shown in Fig. \ref{fig:testDrive}, as it is based on an COTS mobility scooter.  For instance fleets of OpenPodcars might one day transport people over the last mile from the train station to their office, as a low cost electric taxi service. This will require more automation software to operate in busy urban environments.
	
	\subsection{Reuse Potential and Adaptability}\label{h.6wkumyl0ejrh}
	
	The OpenPodcar design is intended so that the mechanical, electronics and software components can be easily ported to other vehicles/platforms and only require small changes on the software side to adapt it and fix some parameters specific to the new vehicle requirements. This could include future deeper OSH vehicles as well as additional commercial donor vehicles. Cheaper sensors such as depth cameras or stereo cameras could be used instead of the 3D lidar. Such modifications would typically require an advanced rather than intermediate designer/builder.

	\section{(5) Build Details}\label{h.l8i9vokvs0bj}
	
	\subsection{Availability of Materials and Methods}\label{h.60suejv0jlzi}
	
	The design is made under the CERN-OSH-W licence which allows for the use of commercially available proprietary components such as the off-the-shelf donor vehicle. However the design is intended to be easily modifiable for transfer to other base vehicles, including those which are OSH at lower levels. The PCB can be manufactured by many online PCB manufacturers. The additional mechanical and electronics used are common parts available from standard online vendors. 
	
	\subsection{Ease of Build}\label{h.wg823sgyb1e4}
	
	The vehicle modification requires the use of common hand tools for assembly: spanners, screwdrivers, and pliers. Additionally, a 3D printer is needed to fabricate some components. Basic soldering skills are needed for assembling the PCB. 
	
	\subsection{Operating Software and Peripherals}\label{h.uz77dixfh5i4}
	
	The system requires open source software: Arduino IDE, Ubuntu 16.04, ROS Kinetic, Gazebo, KiCad (PCB Design), ROS GMapping, ROS move\_base, and Velodyne lidar driver. It also requires the Pololu Configuration Utility Manager software which is available gratis from the manufacturer website. The on-board laptop should have minimal specifications of amd64 3GHz quad-core, 8GB RAM, 250Gb hard-disc, USB and Ethernet ports. The system might also work on lower specifications. Step-by-step instructions for installation of these software dependencies, and the new system software components, are provided in the repository.
	
	\subsection{Hardware Documentation and Files Location:}\label{h.nbisrsde6sc3}
	
	\textbf{Archive for hardware documentation, build files and software}
	
	\textbf{Name}: GitHub
	
	%\textbf{Persistent identifier:} e.g. DOI, etc.
	
	\textbf{Project repository:} \url{https://github.com/OpenPodcar/OpenPodcar}
	
	\textbf{Licence:} CERN-OHL-W for hardware design and build instructions; GPL for software source code.
	
	\textbf{Date published:} 09/05/2022
	
	The hardware is structured as two separate formal OSH designs, each licenced as CERN-OSH-W. The first covers all components which are easily transferable to other vehicles without modification. The second contains all components which are specific to the mobility scooter donor vehicle. This structure enables the first design to be used as sub-component of closed products while also preventing closed modifications of it.

	\section{(6) Discussion}\label{h.90jl7wm65t65}
	
	\subsection{Conclusions}\label{h.h3fr33ylzsnh}
	
	OpenPodcar is a multi-purpose hardware and software platform for autonomous vehicle research. It provides the required hardware and software tools to carry out research in this field. The platform has a lower-level stack, a higher-level stack and a simulator for initial testing. It has several safety features to prevent hazards. The general testing carried on the vehicle shows a robust and safe design. Several use cases have been identified and successfully tested. OpenPodcar is open source to allow further improvements and extensions of its capabilities from the community. The replication of this work on a second and later vehicles will help identify build issues and continually improve the documentation.
	
	\subsection{Future Work}\label{h.neocsr410zj}
	
	OpenPodcar is designed to be extensible and modular, both at the hardware and software levels.  As well as improving the current design, the community is warmly invited to create forks such as replacing the mobility scooter with other donor vehicles -- including deeper OSH vehicles -- or extending the ROS stack to more complex on-road self-driving systems such as Autoware.
	
	In the current setup, the lidar has limited perception of obstacles that are too close and not as high as the lidar. This is generally fine, because people or objects would be seen before, but this can be problematic with objects such as desks and chairs that are not detected by the laserscans and can create unexpected collisions. For example, a low-cost alternative to lidar is to use a stereo camera for point cloud sensing. In this option, a StereoLabs ZedCam is mounted similarly on the vehicle roof. 
	
	The design currently uses ROS1 but the robotics community is slowly shifting to ROS2 for its security, real-time control and increased distributed processing features.  OpenPodcar could join this shift when all of its ROS dependencies have themselves completed it.
	
	The donor vehicle currently used it not itself OSH, and it would be interesting and useful to replace it with a more deep OSH vehicle.   Such vehicles would be based on OSH motor drivers and controllers such as the brushed OSMC \cite{robotpoweropen} or brushless ODrive v3.5  \cite{oriveroboticsodrive}.

	\section*{Paper author contributions}\label{h.fy8hbipy6kwe}
	
	Fanta Camara performed the physical podcar automation work including the mechanical design, printed circuit board (PCB), ROS localisation and mapping, path planning, people detector and tracker integration, Gazebo 3D simulation worlds of Lincoln and Leeds university campuses, testing, and wrote the documentation for the physical podcar and  the manuscript. Chris Waltham designed the initial electronics circuit and safety systems, wrote the Arduino code for the speed control and participated in the initial remotely-controlled driving test. Grey Churchill developed the podcar simulator with path planning in ROS/Gazebo and wrote the documentation for the simulator. Charles Fox supervised the work, wrote the manuscript, and wrote some ROS code. The manuscript was improved by comments from all the co-authors.

	\section*{Acknowledgements}\label{h.gu3yyarx72d6}
	
	The authors would like to thank Jacob Lord for creating the vehicle graphical mesh model, Yao Chen for scoping Dubins path methods and the mechanical design, Gabriel Walton for scoping simulation tools, Yicheng Zhang for helping with the 3D printer and many other useful tools for the PCB board, Zak Burrows for the PCB enclosure design and assistance during some autonomous driving tests.

	\section*{Funding statement}\label{h.4u1a7tugh2om}
	
	This project has received funding from EU H2020 grant 723395 interACT, and from InnovateUK  grant 5949683 C19-ADVs.

	\section*{Competing interests}\label{h.q1j1rznb43fl}
	
	The authors declare that they have no competing interests.
	
	\bibliographystyle{plain}
	\bibliography{OpenPodcar}

	\section*{Copyright notice}\label{h.jm5gcqv4g8x0}
	
	\copyright~2022 The Authors. %This is an open-access article distributed under the terms of the Creative Commons Attribution 4.0 International License (CC-BY 4.0), which permits unrestricted use, distribution, and reproduction in any medium, provided the original author and source are credited. See http://creativecommons.org/ licenses/by/4.0/.

\end{document}

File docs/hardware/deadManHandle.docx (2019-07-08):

POD CAR DMH (Dead Man’s Handle) IMPORTANT SAFTEY INFORMATION

Autonomous vehicles can present a significant hazard to people and the environment in which they operated. Damage to surroundings and possible injury to operators and bystanders could result from inappropriate use or malfunction. It is essential that a suitable emergency stop system is implemented in all autonomous vehicles.

Implementing and testing this safety system should be undertaken with the drive wheels of the vehicle raised off of the ground, allowing for checks to be made of the DMH without the risk of the vehicle speeding off out of control.

Given the development platform nature of the OpenPodCar, a safety mechanism which stops the vehicle under fault conditions is a very important part of the design. During the build several methods of implementing this safety system where checked, the one described below is the current solution.

The speed controller on this particular mobility scooter has a dead zone at around 2.5V on its speed input signal which corresponds to drive wheels stopped. Above the dead zone and up to 5V being forward control values and 0V to below the dead zone being reverse control voltages.

These values were checked using a multi meter prior to implementing the Arduino controller and DAC.

This means that if the DAC output from the Arduino where to fail and 0V for example is applied to the mobility scooters speed controller input, the vehicle would respond by spinning the drive wheels backwards at full throttle. This being a dangerous eventuality, it is very important in terms of safety to ensure this situation can not arise.

A two stage approach is used to reduce this risk.

Please refer to the schematic diagram DMH section in conjunction with this description.

Stage 1 – The Relay

A relay is used which interrupts the mobility scooter’s key ignition circuit. If the relay is not energised by the presence of a 5V supply to the Arduino, the vehicles movement is disabled. This effectively ensures that if the Arduino is non-functional, for example its power supply has failed or it has been unplugged from the USB port of the control PC and there is a danger that the DAC is not producing the control systems required voltage, the scooter is automatically disabled by effectively switching it off.

Stage 2 – The DMH Switch

A sturdy push button is used which also interrupts the vehicles key ignition circuit. If the PodCar operator detects any abnormality in operation during operation, he/she simply releases pressure from the DMH switch and the vehicles movement is disabled. The DMH switch is wired in series with the relay in the key ignition circuit ensuring that if both the relay contacts and the DMH switch are closed, this is the only condition where the PodCar movement is active.

The addition of the Relay and the DMH Switch are essential for safe operation, especially where new unproven autonomous control systems are in development.

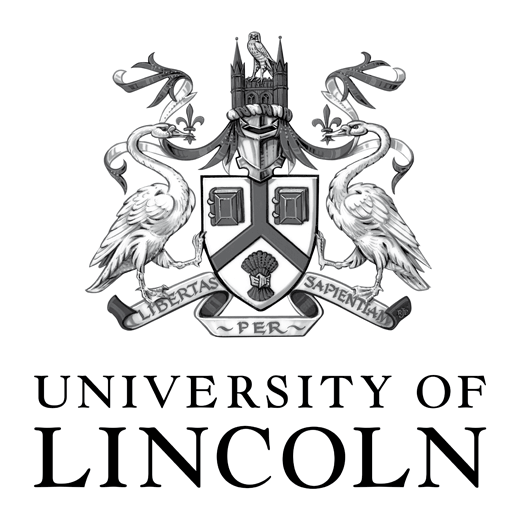
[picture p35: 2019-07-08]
docs/hardware/lincolnbackdrop.gif

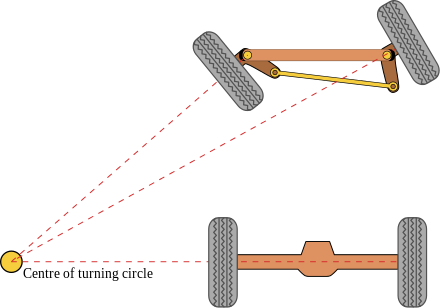
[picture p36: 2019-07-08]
docs/hardware/ackermann2.png

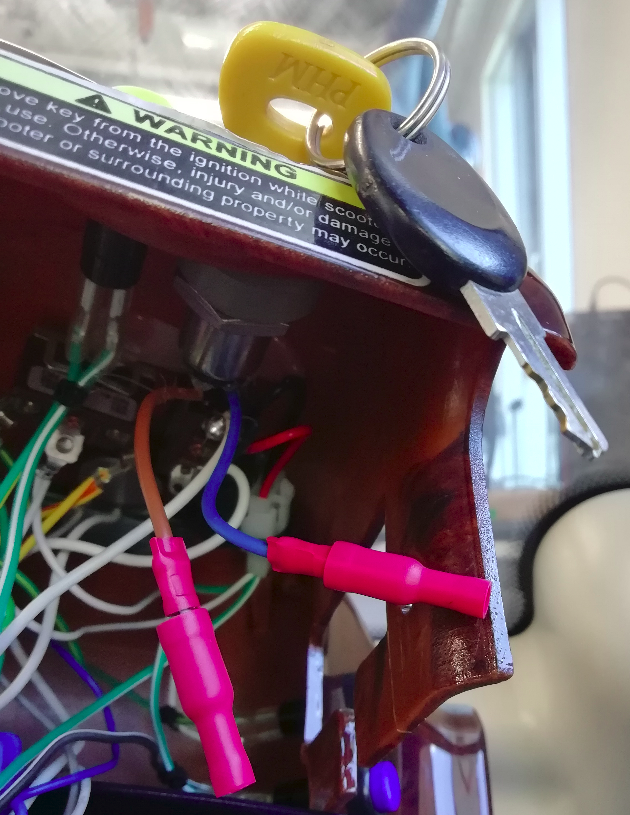
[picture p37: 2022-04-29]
docs/hardware/ignition_key_wires.png

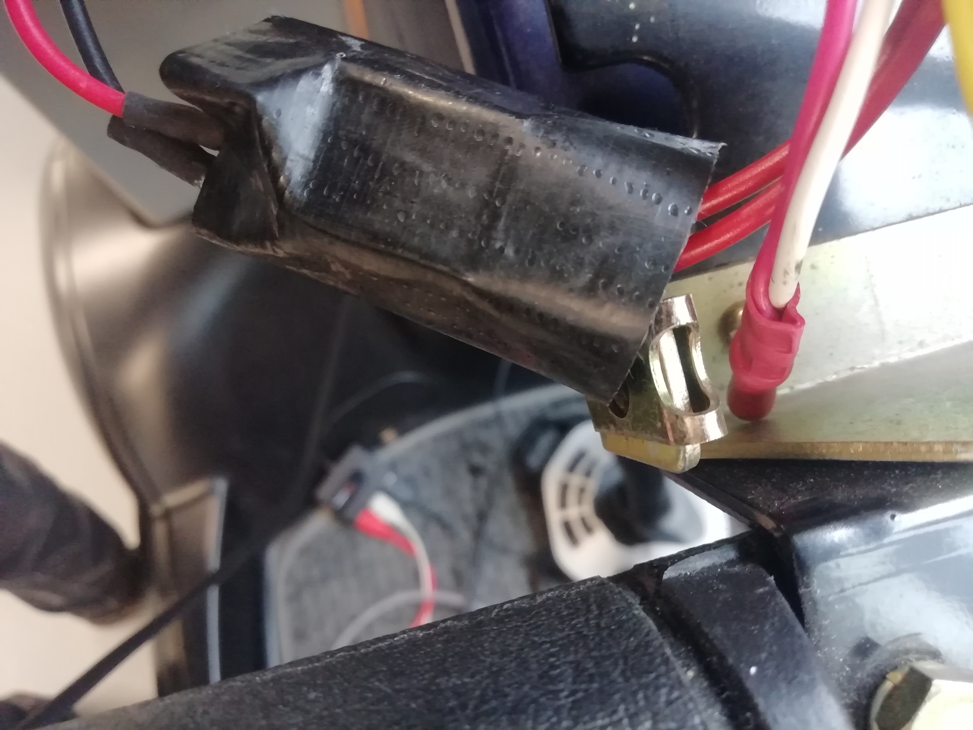
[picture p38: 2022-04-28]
docs/hardware/relay_tape.jpg

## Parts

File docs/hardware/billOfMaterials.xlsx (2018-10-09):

QTY | ITEM | IMAGE | LINK
1 | Arduino UNO |  | https://store.arduino.cc/usa/arduino-uno-rev3
1 | Polulu Motor Driver |  | https://coolcomponents.co.uk/products/jrk-21v3-usb-motor-controller-with-feedback-fully-assembled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
1 | Linear Actuator |  | https://www.ebay.co.uk/i/192674782713
1 | 300W PSU Set to 12V |  | https://www.ebay.co.uk/itm/1pc-10A-300W-DC-DC-Adjustable-Voltage-Step-Down-Converter-Regulator-Module-gib/172847035221
1 | 300W PSU Set to 16V |  | https://www.ebay.co.uk/itm/1pc-10A-300W-DC-DC-Adjustable-Voltage-Step-Down-Converter-Regulator-Module-gib/172847035221
1 | FUSE |  | https://www.ebay.co.uk/itm/BRAND-NEW-STANDARD-INLINE-CAR-FUSE-BLADE-HOLDER-30AMP-12V-SPLASH-PROOF-K265/170976134151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
1 | SWITCH |  | https://www.ebay.co.uk/itm/12V-HEAVY-DUTY-25A-UNIVERSAL-METAL-SPRING-MOMENTARY-ON-OFF-TOGGLE-FLICK-SWITCH/231257116468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
1 | RELAY |  | https://www.ebay.co.uk/itm/5V-DC-1-Channel-LED-Relay-Module-Shield-for-Arduino-Uno-Mega-Raspberry-Pi-Due-UK/161821517993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
1 | DMH PUSH BUTTON |  | https://www.ebay.co.uk/itm/Philmore-30-825-SPST-Hand-Held-Push-Button-Switch-N-O/253746249505?epid=17011384611
1 | MCP4725 DAC |  | https://www.ebay.co.uk/itm/MCP4725-I2C-DAC-Breakout-Module-12Bit-Resolution-Arduino-Raspberry-Pi-UK-/202400708553
1 | Arduino Connection Cables Female to Male 200mm |  | https://www.ebay.co.uk/itm/UK-40-Pin-Dupont-Wire-Line-Ribbon-Jumper-Cables-Breadboard-Arduino-10-20-30CM/323248272555

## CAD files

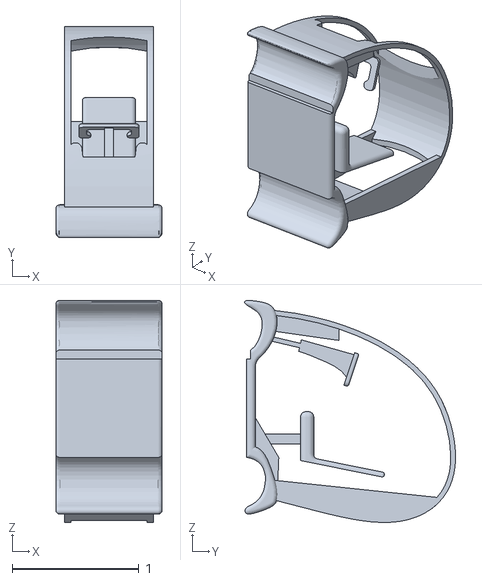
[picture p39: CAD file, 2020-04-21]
catkin_ws/src/podcar/models/podcar/meshes/podcarv3.obj
0.84 x 1.67 x 1.75

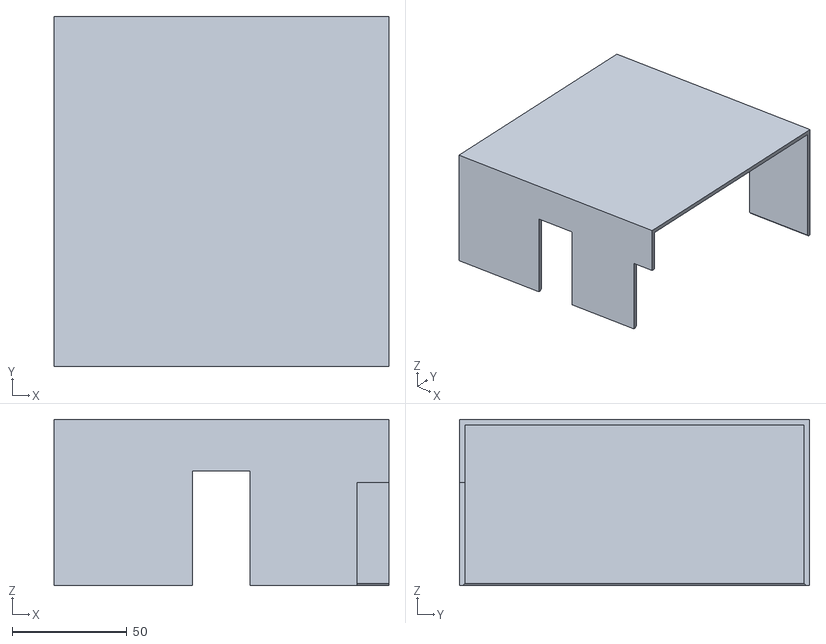
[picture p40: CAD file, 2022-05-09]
physicalVehicleNonRos/3D_parts/PCB_enclosure/pod car electronics case-LidLeft.stl
145.8 x 152.5 x 72.4

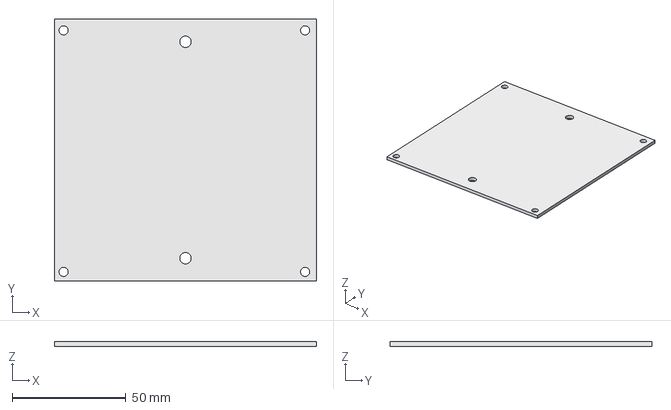
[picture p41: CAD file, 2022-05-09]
physicalVehicleNonRos/3D_parts/VLP16_support.FCStd
115.0 x 115.0 x 2.00 mm

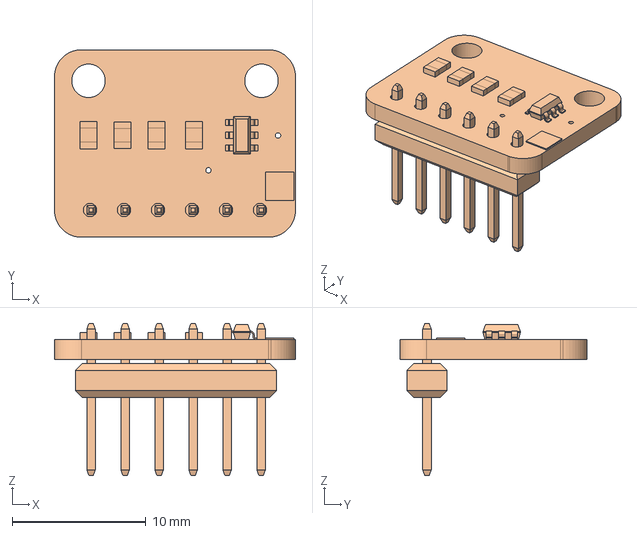
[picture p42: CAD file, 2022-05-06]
physicalVehicleNonRos/PCB/Footprints/Others/adafruit_mcp4725-3D.step
18.0 x 14.0 x 11.4 mm

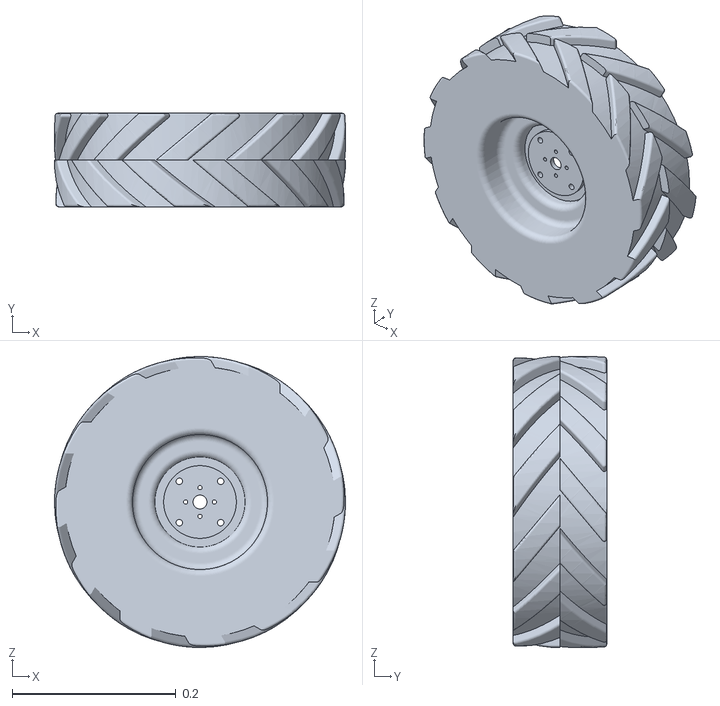
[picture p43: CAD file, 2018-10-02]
catkin_ws/src/podcar/models/podcar/meshes/wheel.stl
0.356 x 0.114 x 0.356

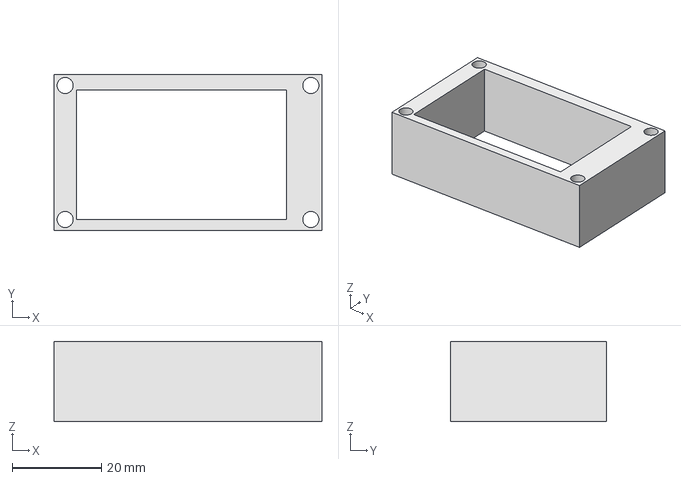
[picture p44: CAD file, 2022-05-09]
physicalVehicleNonRos/3D_parts/LCD_support.FCStd
60.0 x 35.0 x 18.0 mm

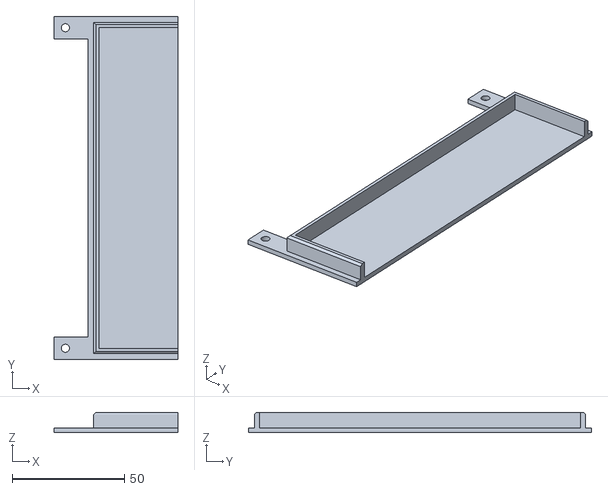
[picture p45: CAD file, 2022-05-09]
physicalVehicleNonRos/3D_parts/PCB_enclosure/pod car electronics case-base plate.stl
55.0 x 152.5 x 9.00

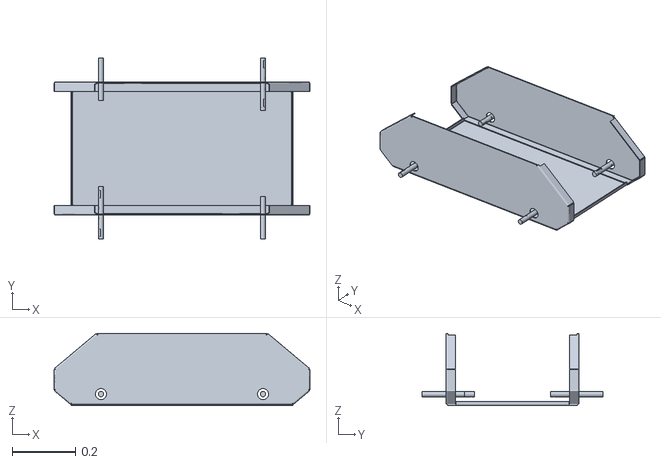
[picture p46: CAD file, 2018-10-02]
catkin_ws/src/podcar/models/podcar/meshes/base_link.stl
0.809 x 0.571 x 0.227

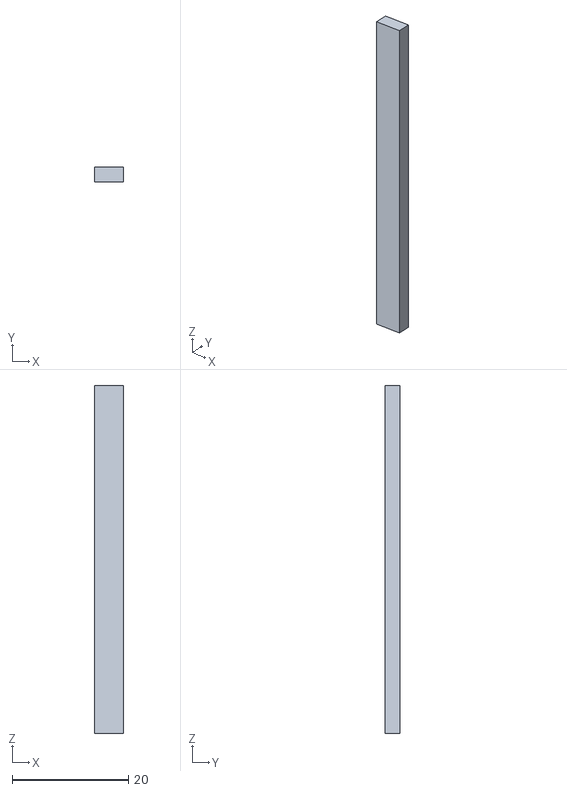
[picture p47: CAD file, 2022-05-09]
physicalVehicleNonRos/3D_parts/PCB_enclosure/pod car electronics case-column support.stl
5.00 x 2.50 x 60.0

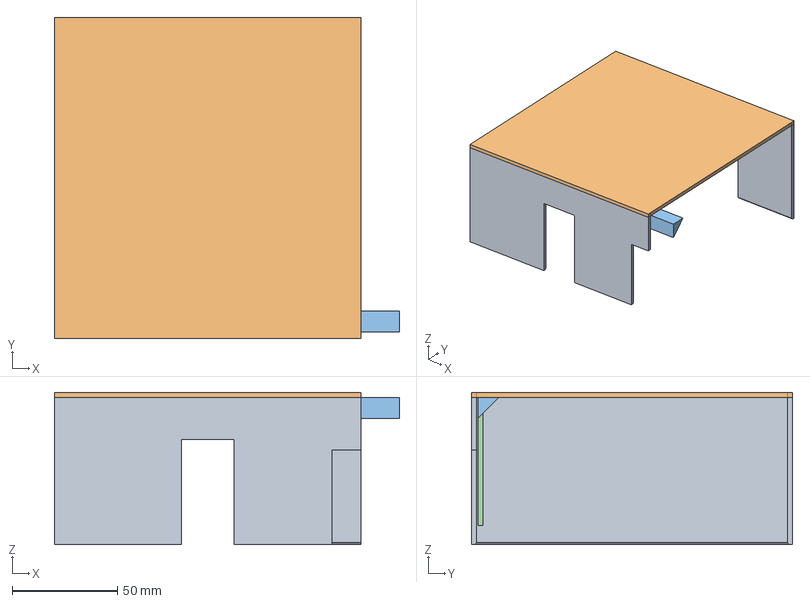
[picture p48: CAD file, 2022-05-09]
physicalVehicleNonRos/3D_parts/PCB_enclosure/pod car electronics case.FCStd
164.0 x 152.5 x 72.4 mm
wallsleft
roofleft
triangle support
column support

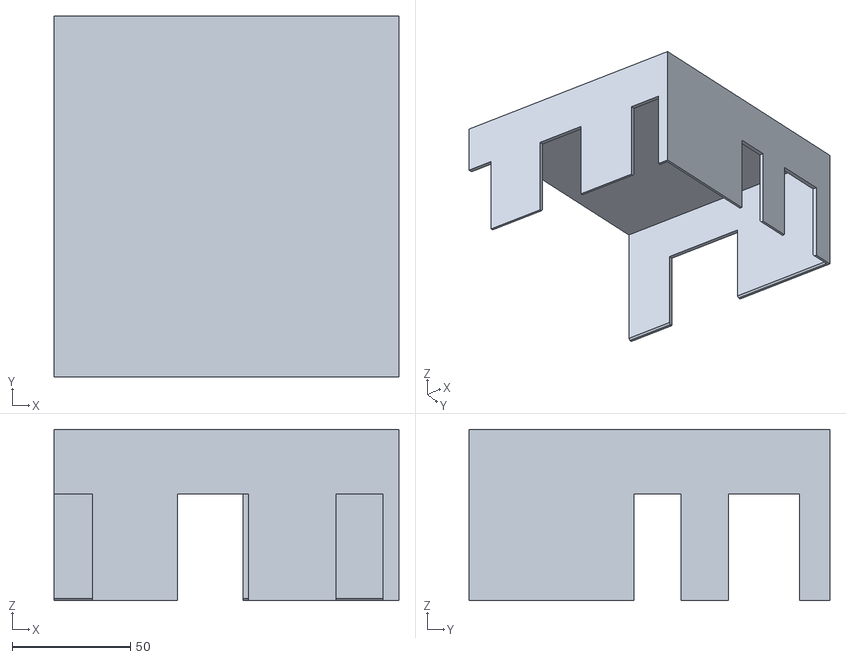
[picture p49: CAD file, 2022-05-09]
physicalVehicleNonRos/3D_parts/PCB_enclosure/pod car electronics case-LidRight.stl
145.8 x 152.5 x 72.4

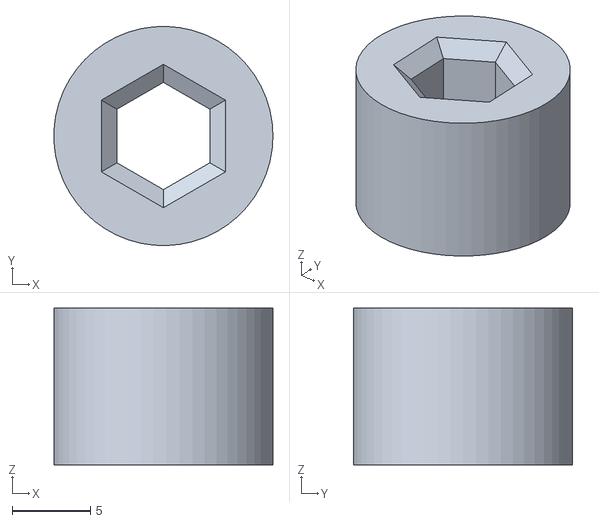
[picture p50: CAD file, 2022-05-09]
physicalVehicleNonRos/3D_parts/PCB_enclosure/pod car electronics case-StandOff Holder.stl
14.0 x 14.0 x 10.0

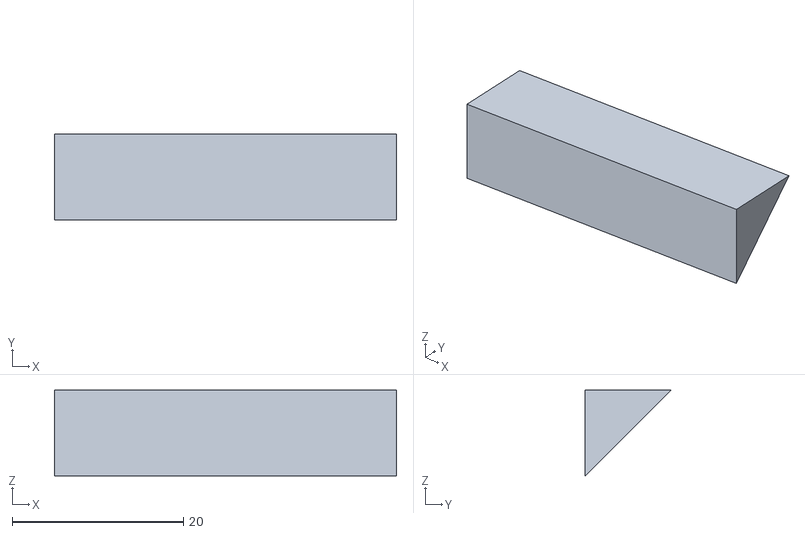
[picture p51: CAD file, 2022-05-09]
physicalVehicleNonRos/3D_parts/PCB_enclosure/pod car electronics case-triangle support.stl
40.0 x 10.0 x 10.0

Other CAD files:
physicalVehicleNonRos/3D_parts/LCD_support.stl
physicalVehicleNonRos/3D_parts/VLP16_support.stl

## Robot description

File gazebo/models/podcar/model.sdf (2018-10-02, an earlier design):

<?xml version="1.0" ?>
<sdf version="1.5">


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

  <model name="podcar">
    <pose>0 0 0.3 0 0 0</pose>


    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
    <link name="base_link">

      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      
	  <inertial>
        <mass>33.855</mass>
        <pose>-0.0856132 -0.000839955 0.238145 0 0 0</pose>
        <inertia>
          <ixx>2.2343</ixx>
          <ixy>-0.023642</ixy>
          <ixz>0.275174</ixz>
          <iyy>3.42518</iyy>
          <iyz>0.00239624</iyz>
          <izz>2.1241</izz>
        </inertia>
      </inertial>

		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
	</link>


    <link name="back_left_wheel">
      <pose>-0.6  0.285475 0.0    0 0 0</pose>
      <inertial>
        <mass>2.6357</mass>
        <pose>0 0 0 0 0 0</pose>
        <inertia>
          <ixx>0.0246688</ixx>
          <ixy>0</ixy>
          <ixz>0</ixz>
          <iyy>0.0246688</iyy>
          <iyz>0</iyz>
          <izz>0.0441058</izz>
        </inertia>
      </inertial>
      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
    </link>
    <joint name="back_left_joint" type="revolute">
      <parent>base_link</parent>
      <child>back_left_wheel</child>
      <axis>
        <xyz>0 1 0</xyz>
        <use_parent_model_frame>true</use_parent_model_frame>
      </axis>
      <physics>
        <ode>
          <limit>
            <cfm>0.000000</cfm>
            <erp>0.900000</erp>
          </limit>
        </ode>
      </physics>
    </joint>



    <link name="back_right_wheel">
      <pose>-0.6 -0.285475 0.0  0 0 0</pose>
      <inertial>
        <mass>2.6357</mass>
        <pose>0 0 0 0 0 0</pose>
        <inertia>
          <ixx>0.0246688</ixx>
          <ixy>0</ixy>
          <ixz>0</ixz>
          <iyy>0.0246688</iyy>
          <iyz>0</iyz>
          <izz>0.0441058</izz>
        </inertia>
      </inertial>
      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
    </link>
    <joint name="back_right_joint" type="revolute">
      <parent>base_link</parent>
      <child>back_right_wheel</child>
      <axis>
        <xyz>0 1 0</xyz>
        <use_parent_model_frame>true</use_parent_model_frame>
      </axis>
      <physics>
        <ode>
          <limit>
            <cfm>0.000000</cfm>
            <erp>0.900000</erp>
          </limit>
        </ode>
      </physics>
    </joint>





  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
    <link name="front_left_pivot">
      <pose>0.6 0.285475 0.0 0 0 0</pose>
      <inertial>
        <mass>2.6357</mass>
        <pose>0 0 0 0 0 0</pose>
        <inertia>
          <ixx>0.0246688</ixx>
          <ixy>0</ixy>
          <ixz>0</ixz>
          <iyy>0.0246688</iyy>
          <iyz>0</iyz>
          <izz>0.0441058</izz>
        </inertia>
      </inertial>
    </link>
    <joint name="front_left_pivot_joint" type="revolute">
      <parent>base_link</parent>
      <child>front_left_pivot</child>
      <axis>
        <xyz>0 0 1</xyz>
        <use_parent_model_frame>true</use_parent_model_frame>
      </axis>
      <physics>
        <ode>
          <limit>
            <cfm>0.000000</cfm>
            <erp>0.900000</erp>
          </limit>
        </ode>
      </physics>
    </joint>

    <link name="front_left_wheel">
      <pose>0.6 0.285475 0.0 0 0 0</pose>
      <inertial>
        <mass>2.6357</mass>
        <pose>0 0 0 0 0 0</pose>
        <inertia>
          <ixx>0.0246688</ixx>
          <ixy>0</ixy>
          <ixz>0</ixz>
          <iyy>0.0246688</iyy>
          <iyz>0</iyz>
          <izz>0.0441058</izz>
        </inertia>
      </inertial>
      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
    </link>
    <joint name="front_left_joint" type="revolute">
      <parent>front_left_pivot</parent>
      <child>front_left_wheel</child>
      <axis>
        <xyz>0 1 0</xyz>
        <use_parent_model_frame>false</use_parent_model_frame>
      </axis>
      <physics>
        <ode>
          <limit>
            <cfm>0.000000</cfm>
            <erp>0.900000</erp>
          </limit>
        </ode>
      </physics>
    </joint>



  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
    <link name="front_right_pivot">
      <pose>0.6 -0.285475 0.0 0 0 0</pose>
      <inertial>
        <mass>2.6357</mass>
        <pose>0 0 0 0 0 0</pose>
        <inertia>
          <ixx>0.0246688</ixx>
          <ixy>0</ixy>
          <ixz>0</ixz>
          <iyy>0.0246688</iyy>
          <iyz>0</iyz>
          <izz>0.0441058</izz>
        </inertia>
      </inertial>
    </link>
    <joint name="front_right_pivot_joint" type="revolute">
      <parent>base_link</parent>
      <child>front_right_pivot</child>
      <axis>
        <xyz>0 0 1</xyz>
        <use_parent_model_frame>true</use_parent_model_frame>
      </axis>
      <physics>
        <ode>
          <limit>
            <cfm>0.000000</cfm>
            <erp>0.900000</erp>
          </limit>
        </ode>
      </physics>
    </joint>



    <link name="front_right_wheel">
      <pose>0.6 -0.285475 0.0 0 0 0</pose>
      <inertial>
        <mass>2.6357</mass>
        <pose>0 0 0 0 0 0</pose>
        <inertia>
          <ixx>0.0246688</ixx>
          <ixy>0</ixy>
          <ixz>0</ixz>
          <iyy>0.0246688</iyy>
          <iyz>0</iyz>
          <izz>0.0441058</izz>
        </inertia>
      </inertial>
      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
    </link>
    <joint name="front_right_joint" type="revolute">
      <parent>front_right_pivot</parent>
      <child>front_right_wheel</child>
      <axis>
        <xyz>0 1 0</xyz>
        <use_parent_model_frame>false</use_parent_model_frame>
      </axis>
      <physics>
        <ode>
          <limit>
            <cfm>0.000000</cfm>
            <erp>0.900000</erp>
          </limit>
        </ode>
      </physics>
    </joint>

-->

  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
    <link name="trackingrod">
      <pose>0.5 0 0.0 0 0 0</pose>
      <inertial>
        <mass>2.6357</mass>
        <pose>0 0 0 0 0 0</pose>
        <inertia>
          <ixx>0.0246688</ixx>
          <ixy>0</ixy>
          <ixz>0</ixz>
          <iyy>0.0246688</iyy>
          <iyz>0</iyz>
          <izz>0.0441058</izz>
        </inertia>
      </inertial>
      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
    </link>
	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
    <joint name="tracking_right_pivot_joint" type="revolute">
      <parent>trackingrod</parent>
      <child>front_right_pivot</child>
	  <pose>-.1 0 0 0 0 0 </pose>
      <axis>
        <xyz>0 0 1</xyz>
        <use_parent_model_frame>false</use_parent_model_frame>
      </axis>
      <physics>
        <ode>
          <limit>
            <cfm>0.000000</cfm>
            <erp>0.900000</erp>
          </limit>
        </ode>
      </physics>
    </joint>
    <joint name="tracking_left_pivot_joint" type="revolute">
      <parent>trackingrod</parent>
      <child>front_left_pivot</child>
	  <pose>-.1 0 0 0 0 0 </pose>
      <axis>
        <xyz>0 0 1</xyz>
        <use_parent_model_frame>false</use_parent_model_frame>
      </axis>
      <physics>
        <ode>
          <limit>
            <cfm>0.000000</cfm>
            <erp>0.900000</erp>
          </limit>
        </ode>
      </physics>
    </joint>



    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
       <plugin name="libpodcarGazeboROSPlugin.so" filename="~/podcar/gazebo/plugins/libpodcarGazeboROSPlugin.so">
          <updateRate>10.0</updateRate>
       </plugin>





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


  </model>
</sdf>

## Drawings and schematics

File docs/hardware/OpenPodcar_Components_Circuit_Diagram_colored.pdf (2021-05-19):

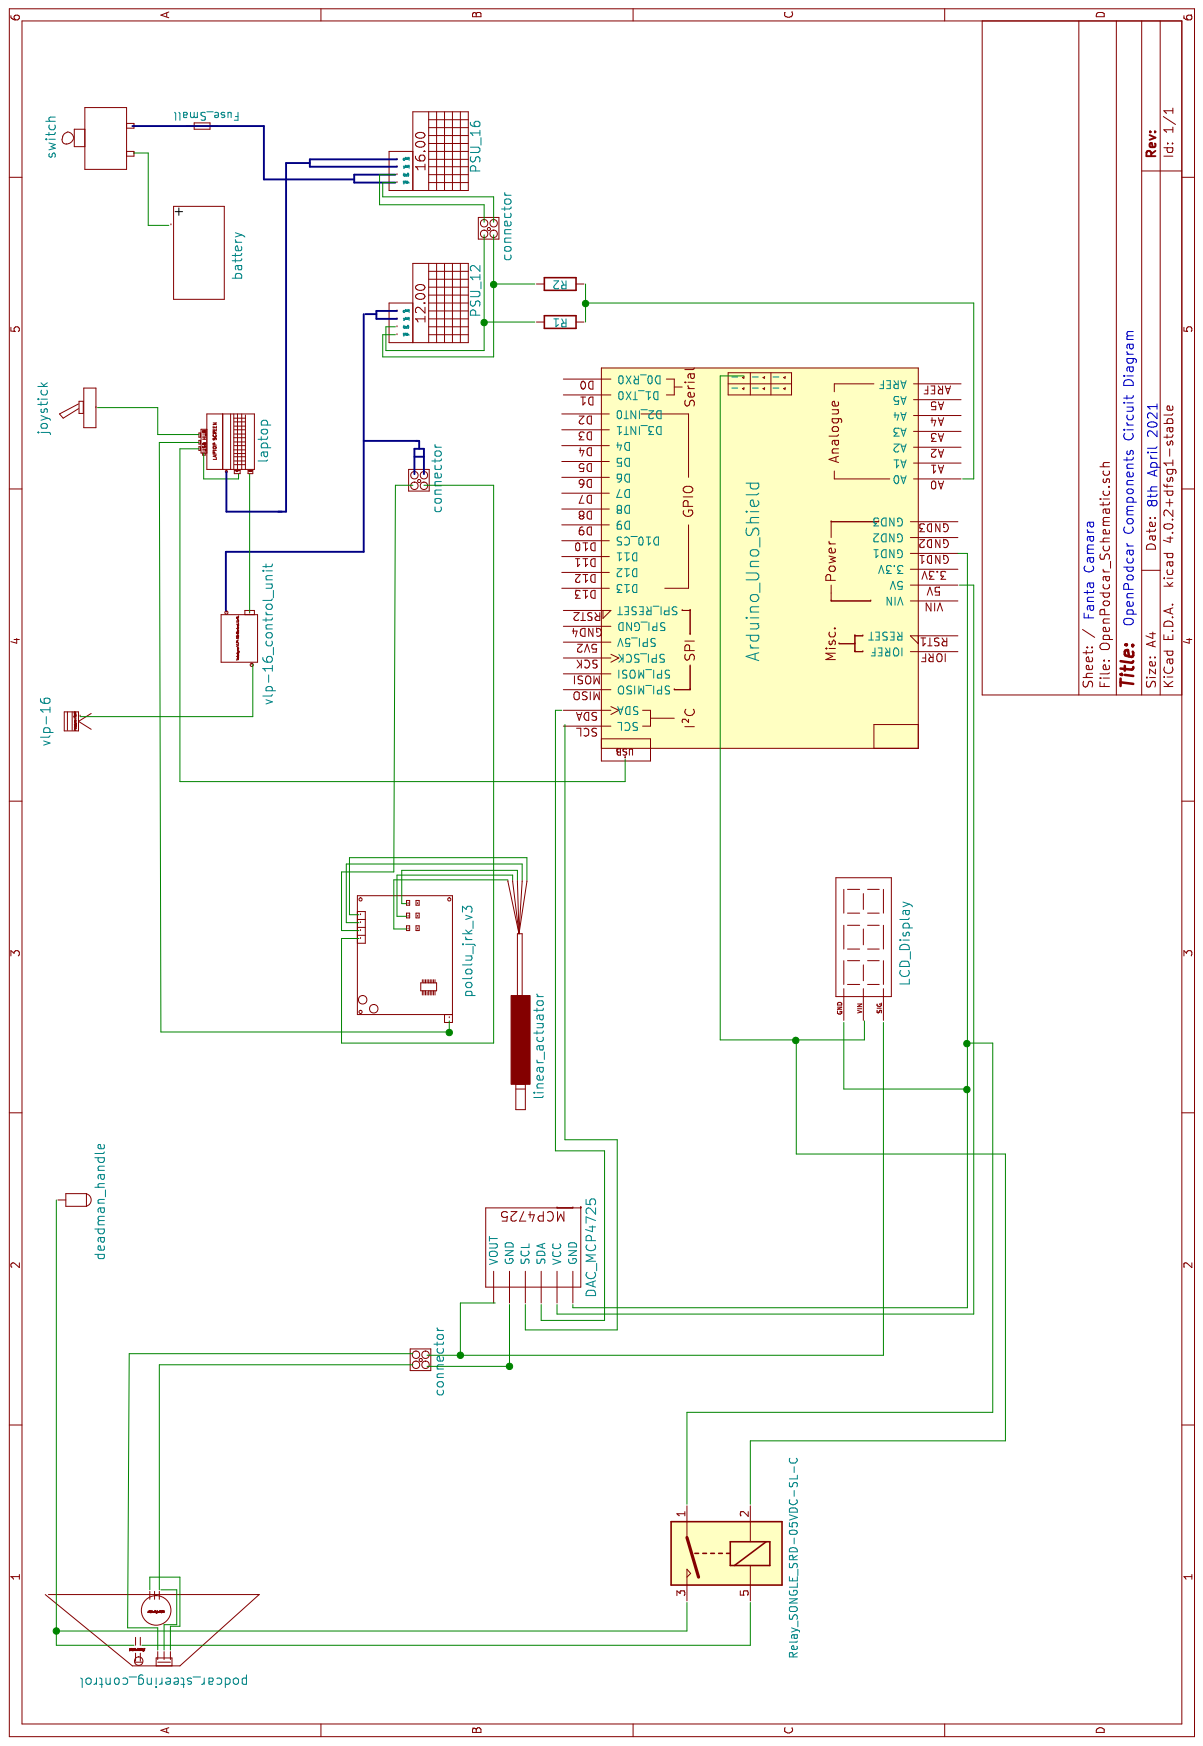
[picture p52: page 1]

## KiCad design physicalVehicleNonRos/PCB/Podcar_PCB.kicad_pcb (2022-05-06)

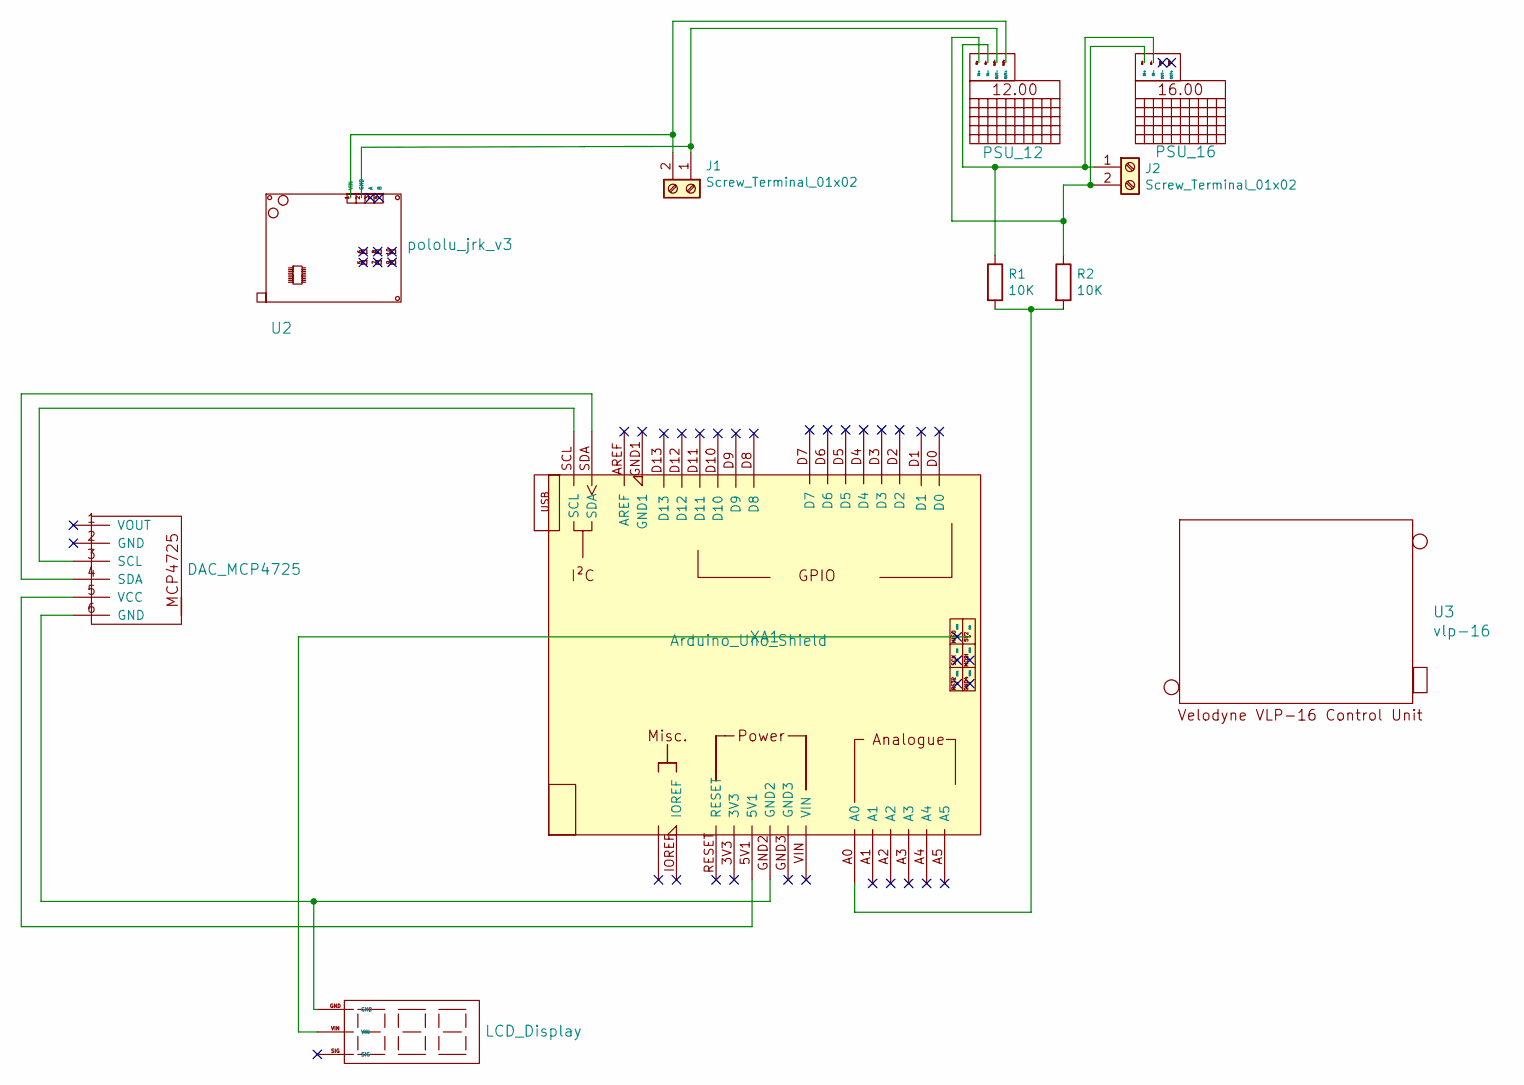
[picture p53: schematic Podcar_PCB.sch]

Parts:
J1, J2: Screw_Terminal_01x02; TerminalBlock_TE_282834-2_1x02_P2.54mm_Horizontal
R1, R2: 10K; R_Axial_DIN0204_L3.6mm_D1.6mm_P7.62mm_Horizontal
U1: DAC_MCP4725; adafruit_mcp4725-fp
U2: pololu_jrk_v3; pololu_jrk21v3
U3: vlp-16; VLP16
U4: LCD_Display
U5: PSU_12; dc_buck_converter-fp
U6: PSU_16; dc_buck_converter-fp
XA1: Arduino_Uno_Shield

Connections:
unnamed: J1.1, U2.2 (GND), U5.OUT-
unnamed: J1.2, U2.1 (VIN), U5.OUT+
unnamed: J2.1, R1.1, U5.IN-, U6.IN-
unnamed: J2.2, R2.1, U5.IN+, U6.IN+
unnamed: R1.2, R2.2, XA1.A0
unnamed: U1.3 (SCL), XA1.SCL
unnamed: U1.4 (SDA), XA1.SDA
unnamed: U1.5 (VCC), XA1.5V1
unnamed: U1.6 (GND), U4.GND, XA1.GND2
unnamed: U4.VIN, XA1.5V2

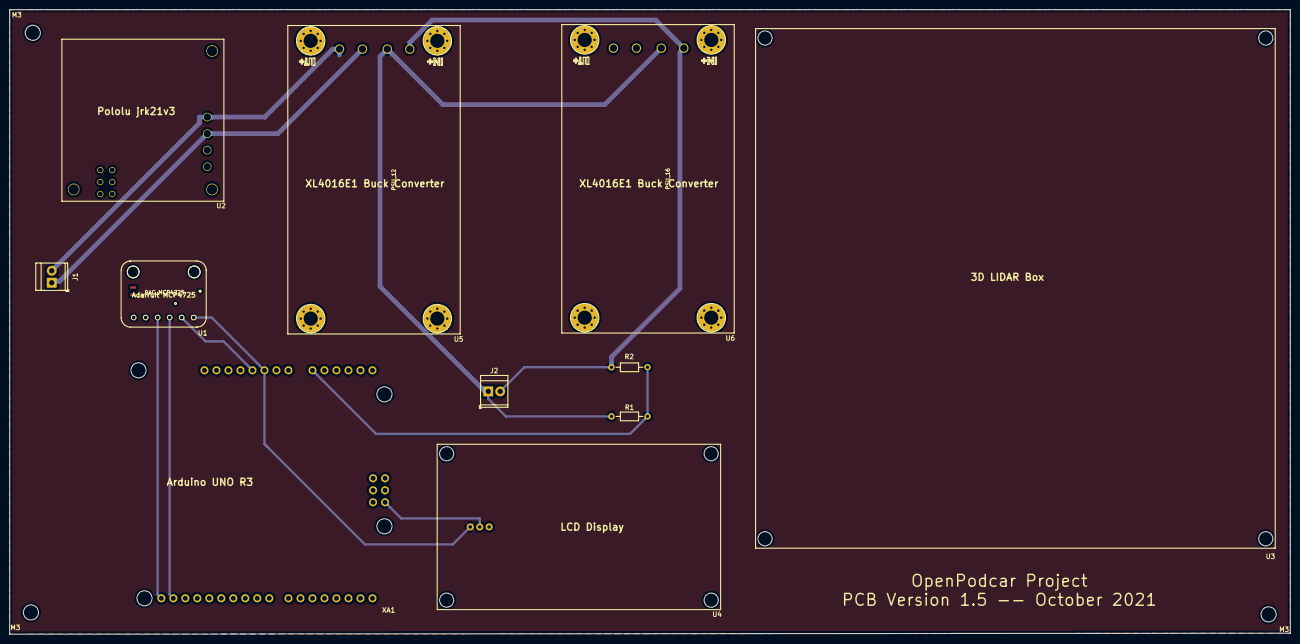
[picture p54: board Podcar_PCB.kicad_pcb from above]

Board: 2 copper layers, 271.1 x 132.2 mm, 14 parts (1 on the bottom side), 10 nets.

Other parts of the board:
M3, M3#2, M3#3: MountingHole_3.2mm_M3

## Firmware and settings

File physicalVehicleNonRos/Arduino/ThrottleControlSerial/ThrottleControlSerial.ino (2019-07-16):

/*****************FA*********************************************************/
/*!
    @file     MobilityScooterThrottle.pde
    @author   Chris Waltham - 24-07-2018

    This Code allows a user to control the throttle circuit of a mobility scooter.

    The DAC use the following address.
    MCP4725A0 address is 0x60 HEX
    
*/
/**************************************************************************/
#include <math.h>
#include <Wire.h>                     // include the Wire Library - needed to communicate with the DAC
#include <Adafruit_MCP4725.h>         // inlcude the DAC library - contains the comms protocol needed to communicate with the DAC

Adafruit_MCP4725 Throttle;            // instantiate a DAC instance called Throttle.

const String FA = "FA";               // ForwardAft Command, format FA:128, colon then byte value for axis 0 to 255, must be terminated with \r\n (carriage return, newline)
const String ST = "ST";               // STOP       Command, format ST, no parameter,  must be terminated with \r\n (carriage return,newline)
const String BV = "BV";               // Battery Voltage       Command, format BV, no parameter,  must be terminated with \r\n (carriage return,newline)

const float RATIO = 0.0537;  // 0.052;              // potential divider ratio found as ratio 0.052 = 55/1023 - 0.0015 

const int analogPin = A0;
int sensorValue = 0;
float batteryVoltage = 0.0;
 
float DACSupplyVoltage        = 5.00; //Included for information only. Could be used to calculate the desired DAC voltage for any DAC Value.

word DACCentre                = 1679;  // new DAC value found in July 2019 -- Charles & Fanta
//word DACCentre                = 1887; // The DAC value which allows the Scooter to switxh on without error or complaint.  
word DAC_Upper_LIMIT          = 2519; // DO NOT CHANGE - COULD DAMAGE SCOOTER CIRCUIT
word DAC_Lower_LIMIT          = 1000; // DO NOT CHANGE - COULD DAMAGE SCOOTER CIRCUIT 
word DACFullScale             = 4095; // 12bit DAC

word ThrottleDACValue         = DACCentre; //Value for ThrottleDACValue after reset/powerup

int ForeAftSerialCmdValue = (int)DACCentre; //Used to calcuate DAC values based on incoming PC parameter values 

bool commandReceived = false;               // Flag to tell non interupt time code to execute newly recieved commands
String fromPC        = "";                  // a String to hold incoming data, no data recieved yet so initialise empty

void setup(){
  
  // Initialise the system
  
  fromPC.reserve(100);                            // Reserve 100 bytes of memory for our serial buffer
  Throttle.begin(0x60);                           // Initialise I2C communications to the DAC board address HEX 60
  delay(100);                                     // Wait 100ms    
  Throttle.setVoltage(ThrottleDACValue, false);   // Set Initial voltage of DAC to the Centre Value.
  Serial.begin(9600);                           // Start the serial port connection to the PC 115200 baud (toggle DTR for remote reset)
  delay(100);                                     // Wait 100ms
  Serial.println("Car Throttle");                 // Announce the controller to the PC  
}

void loop()
{
  
 if(commandReceived == true)                      // This code is executed in non interupt time only when a new command has been recieved                                               // A new command has been recieved when a \n or \r character is recieved.
   processSerialCommand(fromPC);                  // Process the command
   
 
}
 
void UpdateDACs(void)
{            
    Throttle.setVoltage(ThrottleDACValue, false);    //Update the DAC setting.      
}

void serialEvent()                                   // As new characters are recieved by the USART hardware an interupt will fire which executes this code
{                                                    // This code is executed asynchronously in insterupt time.
  if (Serial.available())                            // Check there are characters available.
  {
     char c = Serial.read();                         // read the next available character from the USART buffer
     
     if ((c == '\n' || c == '\r') && fromPC.length() > 0) // check for a line terminator
     {
        fromPC.toUpperCase();                             // converto the command string to upper case
        commandReceived = true;         // set the command pending flag. This tells non interupt time code to execute the command proccesor code. (see: loop() above)
    
     }
     else if (c != ' ' && c != '\n' && c !='\r')          // Ignore spaces.
     {
        fromPC += c;                                      // if the character is not a space, a \n or \r concatenate the character to the fromPC string - build the command charater by character
     }                                                    // This funtion perrforms, in interupt time, a non blocking read of the serial buffer.
  }
}

void processSerialCommand(String command)                 // Simple command processing from the PC to the Scooter Controller - Each command is echoed back to PC along with calucated percentage and DAC value on one lime.
{
                                              // Clear the incoming buffer - current command is passed in 'command' command variable which free's the fromPC variable, so clear it in case more characters are placed in it during interupt time.
                                                     // This may happen now becuase Process Serial Command is now executed in non interupt time.
     
   if (command.startsWith(FA))                            // Is this a FA command? (abbreviation for ForeAft)
   {
       Serial.print(command);                             // Echo the current command to the PC
       Serial.print(" ");
       ForeAftSerialCmdValue = command.substring(3).toInt();       //Extract the value from the command. Structure is 'FA:byte' 0-255, 8 bit throttle value, 127 is the centre value
       float percentageThrottle;       
       percentageThrottle = (float) ForeAftSerialCmdValue / 255;   // Calculate a percentage throttle from the incoming command value
       Serial.print(percentageThrottle);                           // Echo the commanded percentage throttle setting to the PC
       Serial.print(" ");
       ThrottleDACValue =  DAC_Upper_LIMIT * percentageThrottle;   // Calculate based on the DAC Upper Limit const - the value of the command in terms of DAC values (Range the incoming value into 12bits)
       
       if(ThrottleDACValue >= DAC_Lower_LIMIT && ThrottleDACValue <= DAC_Upper_LIMIT) // check the resulting DAC value is higher than the lower limit and lower than the higher limit consts definitions.
         {
          UpdateDACs();                                                               // Call the update DAC funstion to apply the new voltage at the DAC
          Serial.println(ThrottleDACValue);                                           // Echo the new DAC value to the PC
         }
       else
        Serial.println("DAC LIMITS EXCEDED - THROTTLE SETTING UNCHANGED");            // if limits check fails - echo to PC the error
   }
   else if (command.startsWith(ST))                                                   // is the command ST - i.e. STOP
   {
       Serial.print(command);                                                         // Echo the command to STOP
       Serial.print(" ");
       Serial.println("STOP");              
       ThrottleDACValue = DACCentre;                                                  // STOP means set the DAC to the centre position so set the DAC Value to Centre
       UpdateDACs();                                                                  // Call update DAC with the new centre (STOP) value.
   }
   else if (command.startsWith(BV))
   {
      sensorValue = analogRead(analogPin);
      batteryVoltage = sensorValue*RATIO;
      
      Serial.print(command);
      Serial.print(" BV:");
      Serial.println(batteryVoltage);
  
   }
   
  fromPC = "";
  commandReceived = false;                       // Clear the command pending flag.
   
}

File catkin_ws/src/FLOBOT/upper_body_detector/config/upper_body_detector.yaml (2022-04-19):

#=====================================
# Upper body detector parameters
#=====================================
upper_body_detector: 
    #=====================================
    # Distance Range Accepted Detections
    #=====================================
    distance_range_accepted_detections: 7 # up to what distance detections are kept. All detections after that distance are rejected
    
    #=====================================
    # ROI
    #=====================================
    inc_width_ratio: 0.2
    inc_height_ratio: 0.0
    region_size_threshold: 10
    
    #======================
    # Freespace 
    #======================
    # parameteters for occupancy Map computation
    
    # these parameter define the number of bins for the occupancy histogram
    freespace_scaleZ: 20 
    freespace_scaleX: 20
    
    freespace_minX: -3
    freespace_minZ: 0
    freespace_maxX: 3
    freespace_maxZ: 7
    freespace_threshold: 500
    freespace_max_depth_to_cons: 7
    
    #====================================
    # Detector
    #====================================
    # parameters upper body detector
    evaluation_NMS_threshold_LM: 0.25 # lowering this parameter will reduce the number of false positives! Keep in mind this is distance!
    evaluation_inc_height_ratio: 0.2  # parameter for increasing the size of ROI which is then scanned by the depth template
    
    # <<< these parameters are only relevant if you want to perform multi-scaling, evaluation_nr_scales > 1
    evaluation_stride: 3 
    evaluation_scale_stride: 1.03
    evaluation_nr_scales: 1
    evaluation_inc_cropped_height: 20
    evaluation_greedy_NMS_overlap_threshold: 0.3
    evaluation_greedy_NMS_threshold: 0.5 # default 0.25
    # >>>
    
    # scanning corridor, which means for each ROI we scan it with the depth template starting from min_height (in meters) for up to max_height
    max_height: 2.1
    min_height: 1.0
    
    #======================
    # World scale
    #======================
    WORLD_SCALE: 1.0
    
    #===========================
    # height and width of images
    #===========================
    dImWidth: 640
    dImHeight: 480
    
    #====================================
    # Number of Frames / offset
    #====================================
    numberFrames: 1000000
    nOffset: 0
    
    #====================================
    # Size of Template
    #====================================
    template_size: 30

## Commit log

2018-10-02 init add files
    [base_link.stl, model.sdf, wheel.stl]
2018-10-02 changes paths
    [model.sdf]
2018-10-09 add arduino
2018-10-09 add hardware diags from chris
    [billOfMaterials.xlsx]
2019-07-05 add ros catkin
    [config.txt]
2019-07-05 add old
    [1.sdf, 2.sdf, 3.sdf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]
2019-07-05 add steer limits
    [billOfMaterials.xlsx]
2019-07-05 move notes to docs
    [config.txt]
2019-07-08 chris schematics
2019-07-10 add chris latest Arduino code from email
2019-07-11 move live catkin to git
    [config.txt]
2019-07-16 update arduinbo code for battery value BV cmd
2019-07-16 new blocking arduino ros controller
2020-03-23 Reorganised file structure, added .gitignore for build generated files
    [base_link.stl, model.sdf, wheel.stl]
2020-03-23 remove files and update .gitignore, new build instructions to follow
    [base_link.stl, model.sdf, wheel.stl]
2020-04-02 Working on getting front wheels to turn to desired angle in gazebo plugin.
    [model.sdf]
2020-04-06 Successfully implemented PID controller for steering! TODO: set max turning angles and adjust friction on front wheels
    [model.sdf]
2020-04-07 Add pretty mesh to sim and get joystick working in simulation!
    [model.sdf]
2020-04-08 fix typo in topic name and commit mesh
    [joystick2speedms.py]
2020-04-08 commit mesh for real this time
    [podcarv3.obj]
2020-04-08 Update mesh, remove wheels
    [model.sdf, podcarv3.obj]
2020-04-08 Add node to handle twist messages published to 'cmd_vel' and republish to speed_meterssec and wheelAngleCmd
2020-04-08 final(tm) tweaks to wheel frictions
    [model.sdf]
2020-04-08 joystick.launch for ease of starting sim with joystick controls when needed
    [model.sdf]
2020-04-09 Added kinect as placeholder sensor (needed for move_base) and created transform publisher
    [model-1_2.sdf, model-1_3.sdf, model-1_4.sdf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]
2020-04-13 Add parameters for move_base modules and fix tf orientations
    [joystick2speedms.py, podcar_tf_broadcaster.py]
2020-04-15 Tweaking to teb parameters
    [model.sdf]
2020-04-16 tidy physical vehicle code
    [config.txt, podcarv3.obj]
2020-04-21 Remove redundant gazebo folder and clean up gazebo plugin code
    [podcarv3.obj]
2020-04-27 rm old gazebo version
    [1.sdf, 2.sdf, 3.sdf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]
2020-04-27 rm old cad design
2020-04-27 add into material to paper
2021-05-19 Added complete electronic circuit diagram and edited some texts
2021-11-22 Added BOM and physical podcar configuration in README and edited paper
2021-12-17 Added odometry publisher and sim2real launch file, modified paper and README file
2021-12-21 Adding modified scripts for sim2real work, kept original scripts for simulator, modified velocity control for arduino commands, edited README file
2021-12-23 Adjusted linear actuator steering and podcar speed
2022-01-02 Ported the paper current text to the latex template of the Journal of Open Hardware
2022-01-05 Fixed move_base params and edited paper
    [odometry_publisher.py, wheelAngle2pololu_sim2real.py]
2022-01-07 Working TEB and move but problem with odometry precision
    [odometry_publisher.py, podcar_tf_broadcaster_sim2real.py, wheelAngle2pololu_sim2real.py]
2022-01-19 Working move_base with full gmapping, fixed odmetry groundtruth to map frame
    [odometry_publisher.py]
2022-01-19 Fixed frequency rate for odometry and arduino communication
    [odometry_publisher.py]
2022-02-04 Included laser scan matcher for more accurate odometry and modified costmaps params for move base and TEB planner: been able to drive autonomously but some obstacles such as walls not avoidded
    [odometry_publisher.py, odometry_publisher_gmapping.py, odometry_publisher_laser_scan.py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]
2022-04-19 Updated Readme file and pushing velodyne folder
    [CloudNode.cfg, TransformNode.cfg, VelodyneLaserScan.cfg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]
2022-04-19 Cropped lidar tripod photo
2022-04-22 Added green circles to lidar tripod photo
2022-04-28 Updated README and adding relay photos
2022-04-29 Updated README and adding switch button, fuse and battery photos
2022-04-29 Updated README and switch button, fuse and battery photo
2022-05-06 Updated README and adding rosnodes for autonomous mode and non-ROS files e.g. pcb, 3D parts etc.
    [LCD_support.stl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]
2022-05-06 Updated README and adding CERN-OHL-W v2 licence
    [config.txt]
2022-05-06 Updated paper and adding Leeds and Lincoln universities' 3D models
    [model.sdf]
2022-05-09 Adding 3D parts for PCB enclosure, LCD display and VLP support
    [LCD_support.FCStd, VLP16_support.FCStd, pod car electronics case-LidLeft.stl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]
